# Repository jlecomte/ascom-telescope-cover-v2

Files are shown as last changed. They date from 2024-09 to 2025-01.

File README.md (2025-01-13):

# ASCOM-Compatible Telescope Cover

I do not charge anything to create and maintain these open-source projects. But if you would like to say "thanks" for this project, feel free to send any amount through Paypal using the button below. I appreciate your support!

(https://www.paypal.com/donate/?hosted_button_id=49UXY8F6VVYFA)

<!-- toc -->

- [Introduction](#introduction)
- [Finished Product](#finished-product)
- [Demo](#demo)
- [Pre-Requisites](#pre-requisites)
- [Hardware / BOM](#hardware--bom)
- [ASCOM Driver](#ascom-driver)
  * [Downloading And Installing The Driver](#downloading-and-installing-the-driver)
  * [Compiling The Driver (For Developers Only)](#compiling-the-driver-for-developers-only)
- [Arduino Firmware](#arduino-firmware)
  * [Microcontroller Compatibility](#microcontroller-compatibility)
  * [Compiling And Uploading The Firmware](#compiling-and-uploading-the-firmware)
  * [Calibration Procedure](#calibration-procedure)
- [Electronic Circuit](#electronic-circuit)
- [3D Model](#3d-model)
- [Using With NINA](#using-with-nina)
- [Known Issues](#known-issues)
  * [Device Access Synchronization](#device-access-synchronization)
- [Ideas For Improvements](#ideas-for-improvements)

<!-- tocstop -->

## Introduction

This repository contains code that allows you to build your own automated telescope cover and spectral calibrator:

* The code for the ASCOM driver (Microsoft Visual Studio 2022 project)
* The code for the Arduino firmware
* The FreeCAD 3D model
* The KiCad project for the electronic circuit

This project is an updated version of [my original ASCOM-compatible telescope cover](https://github.com/jlecomte/ascom-telescope-cover). It brings the following enhancements:

* **Analog Position Feedback:** If you happened to power up my original ASCOM-compatible telescope cover while it was not in its closed position, it would violently close because it assumed that it was in a closed position at startup. This is now fully resolved by using a servo with analog position feedback. Note that this feedback loop needs to be calibrated once.
* **Magnets:** The cover will be held in place (in either open or closed position) by magnets, which means that the servo can be powered off when it is not moving, thereby completely eliminating the possibility of vibrations while imaging.
* **PCB:** This new project uses a PCB that can be manufactured by a company like [PCB Way](https://www.pcbway.com/). This means that the final product is more compact and more reliable than when using a perforated circuit board as in my original project.
* **Spectral Calibrator:** This project includes neon bulbs that can be remotely turned on or off. This is especially useful when doing spectroscopy. **Note:** You could technically modify this project to eliminate this (if you don't need it) or replace it with an EL panel if you would like to create a motorized flat panel. I have no need for this because I have [a wireless flat panel](https://github.com/jlecomte/ascom-wireless-flat-panel) and while I do operate my equipment remotely, it is not located in a remote location (it is in my backyard, but it is nice to be able to fully control it from inside the house, or using a fully automated sequence).
* **Better 3D Model:** This new version comes with a much improved 3D model and the final product is much sturdier than my original version. It also provides a simpler and cleaner attachment method to the OTA.
* **Single Cable:** This new version only requires a USB type C cable connection for both power and data, whereas my original version required two cables (USB type C and 12V power)

## Finished Product

Here is what the finished product looks like:

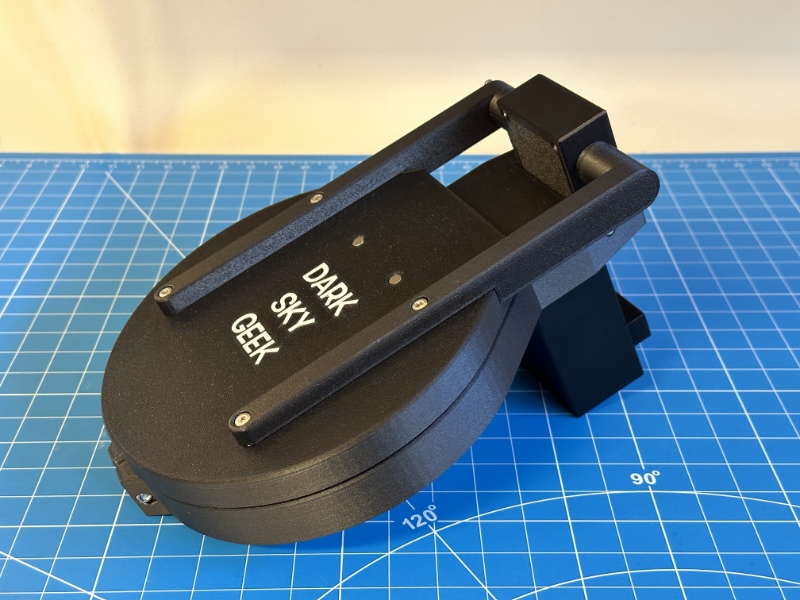
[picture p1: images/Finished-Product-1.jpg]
Finished Product


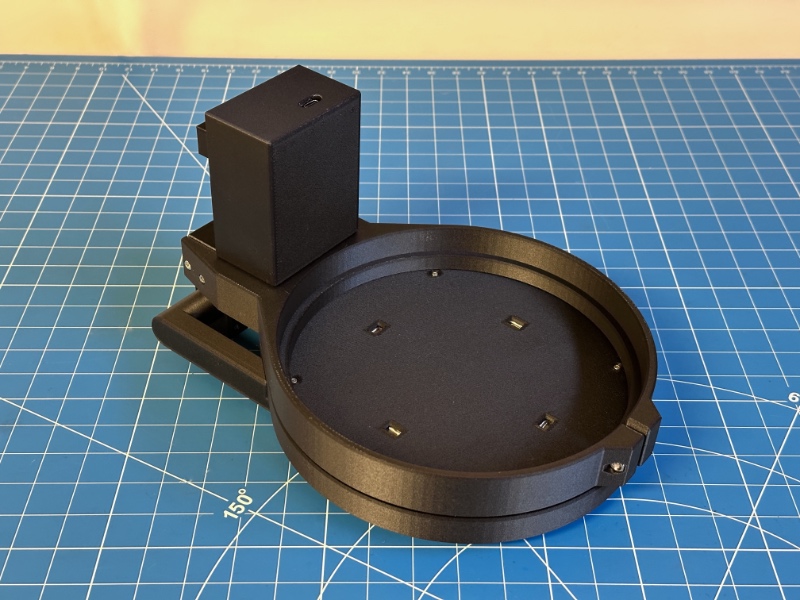
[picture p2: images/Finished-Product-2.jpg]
Finished Product


## Demo

Here is a short demo video of the finished product, hosted on YouTube. Check it out!

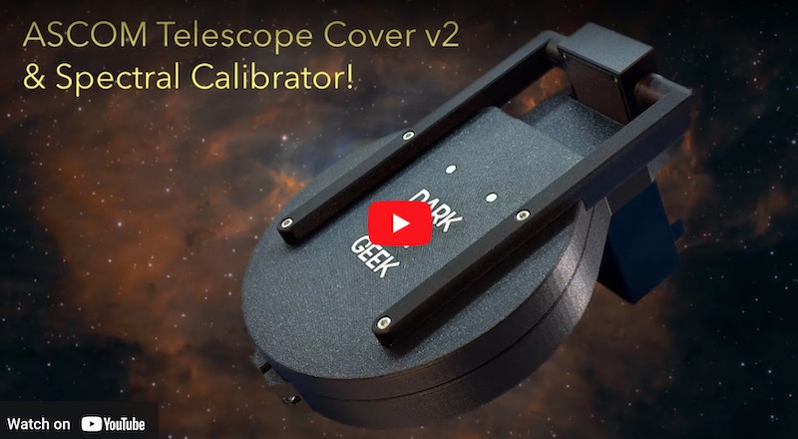
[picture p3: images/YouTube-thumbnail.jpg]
Short demo video of the finished product (https://www.youtube.com/watch?v=r8KIGEcJ2Xw)


## Pre-Requisites

* A Windows computer (Windows 10 or newer)
* [Microsoft Visual Studio](https://visualstudio.microsoft.com/) (FYI, I used the 2022 edition...)
* [ASCOM Platform 6](https://ascom-standards.org/)
* [ASCOM Platform Developer Components](https://ascom-standards.org/COMDeveloper/Index.htm)
* [Arduino IDE](https://www.arduino.cc/en/software)
* [FreeCAD](https://www.freecadweb.org/), a free and open-source 3D parametric modeler
* A 3D printer able to print PETG, and a slicer (I use a Bambu Lab X1C)
* A few basic tools that any tinkerer must own, such as [a breadboard](https://www.amazon.com/dp/B07LG9V8WQ?tag=darkskygeek-20), [a soldering iron](https://www.amazon.com/dp/B08M9B4MP4?tag=darkskygeek-20), [a bench power supply](https://www.amazon.com/dp/B07GCJ5QHF?tag=darkskygeek-20), etc.

## Hardware / BOM

* [Seeeduino XIAO](https://www.seeedstudio.com/Seeeduino-XIAO-Arduino-Microcontroller-SAMD21-Cortex-M0+-p-4426.html) (You can get it quicker from Amazon, but you will have to pay twice as much!)
* [Capacitors](https://www.amazon.com/dp/B07PBQXQNQ?tag=darkskygeek-20)
* [Resistors](https://www.amazon.com/dp/B08FD1XVL6?tag=darkskygeek-20)
* [Diodes](https://www.amazon.com/dp/B08SBTS2KZ?tag=darkskygeek-20)
* [FQP30N06L](https://www.amazon.com/dp/B07WHSD3GJ?tag=darkskygeek-20) (logic-level MOSFET)
* [EL Inverter](https://www.amazon.com/dp/B08Q7CNZ7F?tag=darkskygeek-20)
* [Neon bulbs](https://www.amazon.com/dp/B07CPY6TM5?tag=darkskygeek-20)
* [270° servo motor with analog feedback](https://www.dfrobot.com/product-1709.html)
* [8x2mm magnets](https://www.amazon.com/dp/B077KYBYYY?tag=darkskygeek-20)
* [Brass inserts for 3D printed parts](https://www.amazon.com/dp/B0BDD3865B?tag=darkskygeek-20)
* [Assortment of small metric screws, nuts, and washers](https://www.amazon.com/dp/B08JCKH31Q?tag=darkskygeek-20)

## ASCOM Driver

### Downloading And Installing The Driver

You can install the ASCOM driver by simply running the executable setup file that you will find in the [releases page](https://github.com/jlecomte/ascom-telescope-cover-v2/releases). By default, it places files under `C:\Program Files (x86)\Dark Sky Geek\Telescope Cover V2 ASCOM Driver`.

### Compiling The Driver (For Developers Only)

Open Microsoft Visual Studio as an administrator (right click on the Microsoft Visual Studio shortcut, and select "Run as administrator"). This is required because when building the code, by default, Microsoft Visual Studio will register the compiled COM components, and this operation requires special privileges (Note: This is something you can disable in the project settings...) Then, open the solution (`ASCOM_Driver\TelescopeCoverV2.sln`), change the solution configuration to `Release` (in the toolbar), open the `Build` menu, and click on `Build Solution`. As long as you have properly installed all the required dependencies, the build should succeed and the ASCOM driver will be registered on your system. The binary file generated will be `ASCOM_Driver\bin\Release\ASCOM.DarkSkyGeek.TelescopeCoverV2.dll`.

## Arduino Firmware

### Microcontroller Compatibility

Pretty much all Arduino-compatible boards should work. There is nothing magical about the firmware. However, this was developed for, and tested with a [Seeeduino XIAO](https://www.seeedstudio.com/Seeeduino-XIAO-Arduino-Microcontroller-SAMD21-Cortex-M0+-p-4426.html), so that is what I recommend for this project.

### Compiling And Uploading The Firmware

* If needed, add support for the board that you are using in your project.
* Then, connect your board to your computer using a USB cable, open the sketch file located at `Arduino_Firmware\Arduino_Firmware.ino`, and click on the `Upload` button in the toolbar.

### Calibration Procedure

This is a one-time operation. Disconnect the right arm from the servo. Then, from the Arduino IDE, connect to the device. Using the Arduino IDE serial monitor, type `COMMAND:COVER:CALIBRATE`. This will launch the calibration procedure for the servo analog feedback. Once it has completed, re-attach the right arm to the servo. The device is now ready to be used.

## Electronic Circuit

Here is the KiCad schematics:

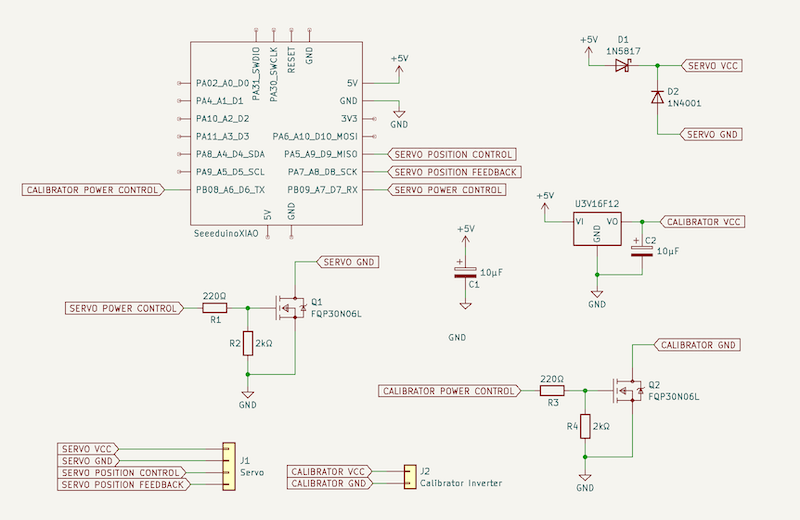
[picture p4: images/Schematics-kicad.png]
KiCad schematics


I very strongly recommend prototyping it first, using a breadboard:

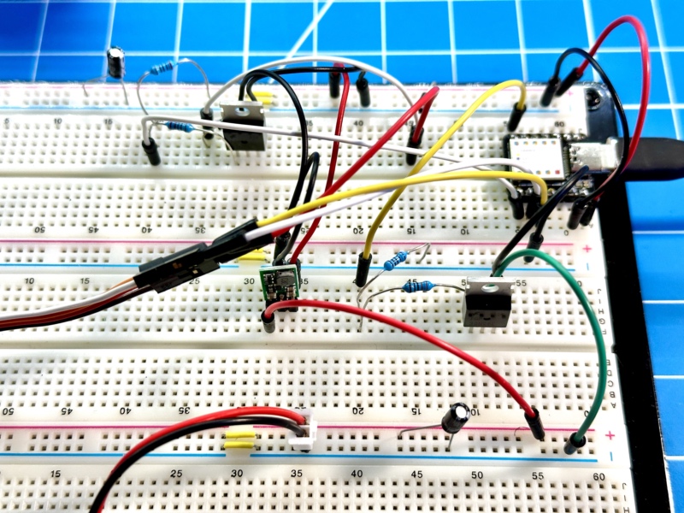
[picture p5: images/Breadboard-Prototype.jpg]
Breadboard prototype


Here is the routed PCB in KiCad:

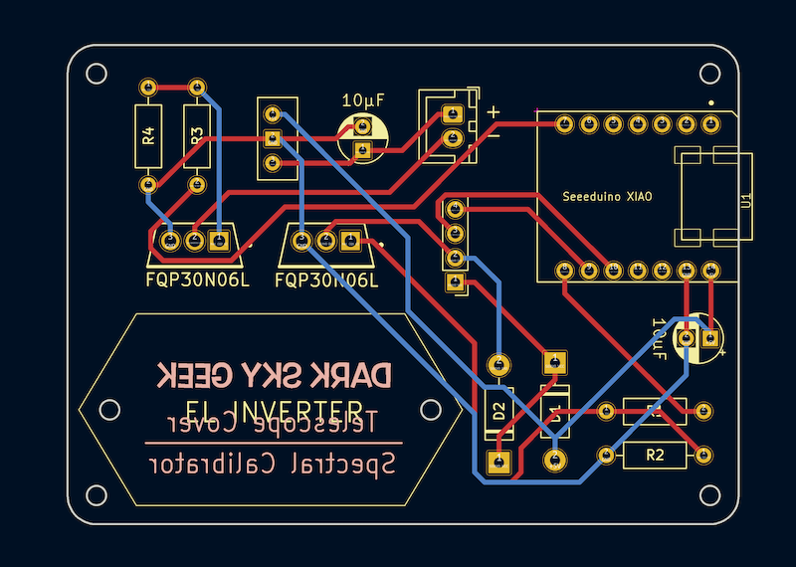
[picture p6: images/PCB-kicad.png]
Routed PCB in KiCad


**Note:** You can directly use [PCBWay.zip](KiCad_Project/PCBWay.zip) to order your PCB from [PCB Way](https://www.pcbway.com/).

Once you've received your PCB and soldered all the components, it should look like the following:

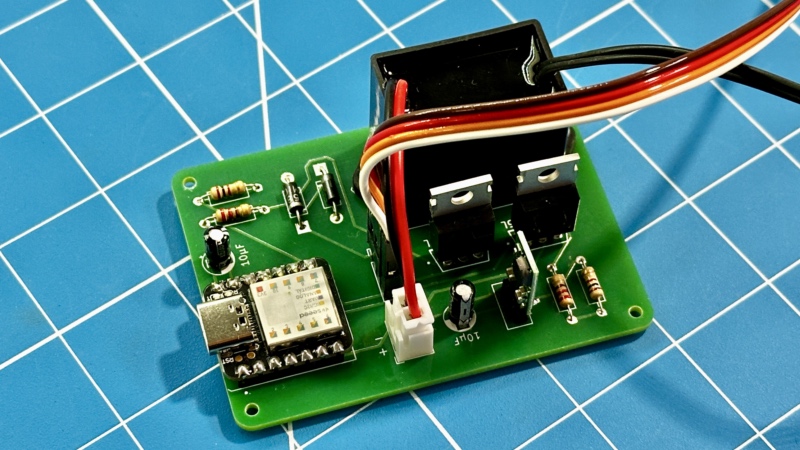
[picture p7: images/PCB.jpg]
Finished PCB


## 3D Model

:warning: **IMPORTANT:** :warning: The 3D model is parametric and will scale within a reasonable range of values for the `OTA Outside Diameter` and `OTA Thickness` pareneters (see the `Parameters` spreadsheet in the 3D model for more details...) However, FreeCAD being FreeCAD, be warned that if you change the value of a parameter multiple times, you may get a model error. Simply close the model without saving it, reopen it, and set the parameter you want to change, e.g., the `OTA Outside Diameter` parameter, to the appropriate value. The model *should* scale properly.

Here is what the 3D model looks like in FreeCAD:

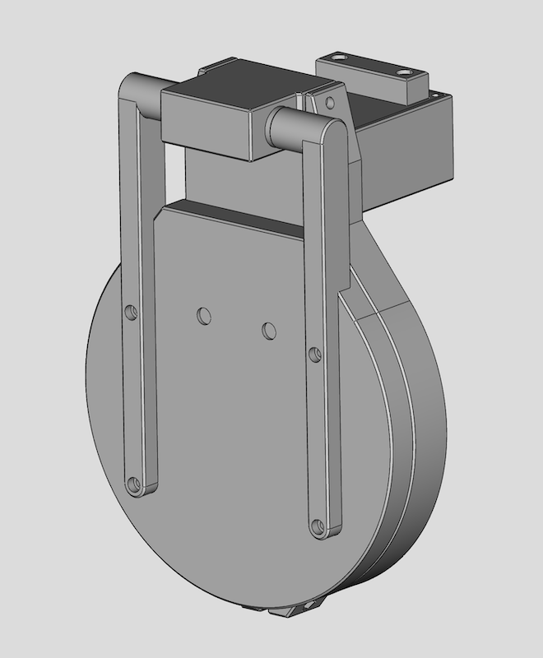
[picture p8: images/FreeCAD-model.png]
FreeCAD model


Once you've updated the model to fit your needs, you can export the parts as STL and print them on your 3D printer.

Here is how the neon bulbs are installed on the back of the cover lid:

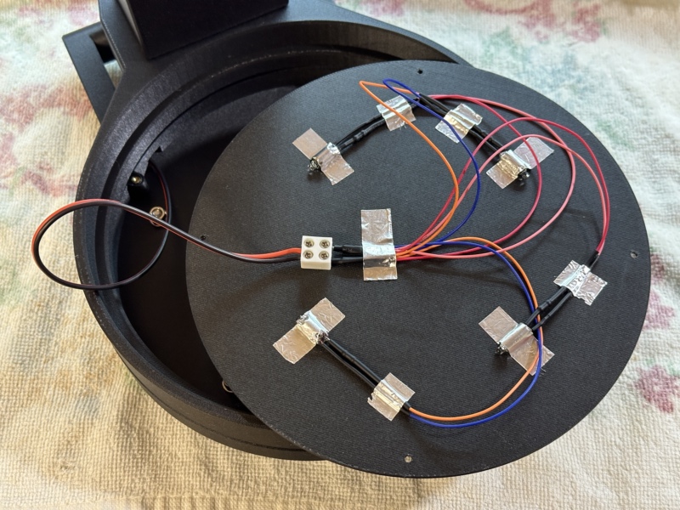
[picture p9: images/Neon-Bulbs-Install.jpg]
Neon Bulbs Install


A 47kΩ resistor is soldered to _each_ bulb, and the 4 x _resistor + bulb_ are wired in parallel (that is critical!)

The wires that power up those bulbs travel through the servo box and the left arm, so they are not directly visible, which makes for a very clean final product.

## Using With NINA

Once you have installed the driver, open NINA, go to the `Equipment` tab and select `Flat Panel`. You should be able to select the `DarkSkyGeek Telescope Cover & Spectral Calibrator` device from the device dropdown:

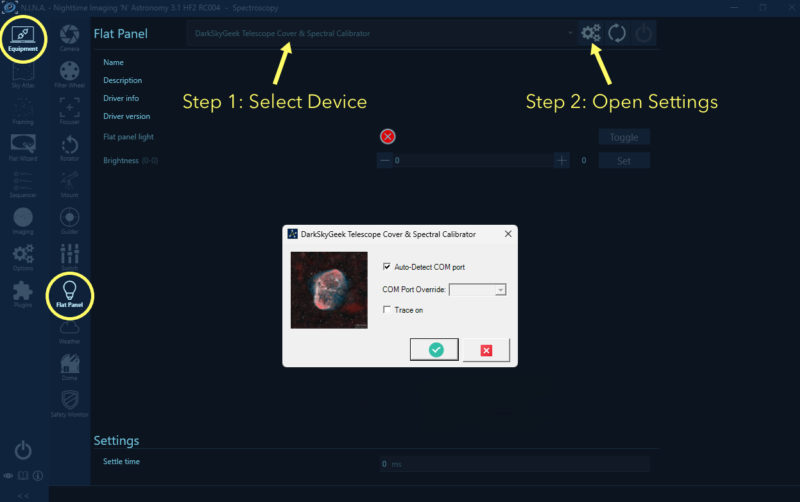
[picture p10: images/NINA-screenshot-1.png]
NINA Screenshot 1


Then, you can connect to the device, and all the standard controls should appear, allowing you to test and use your device. Enjoy!

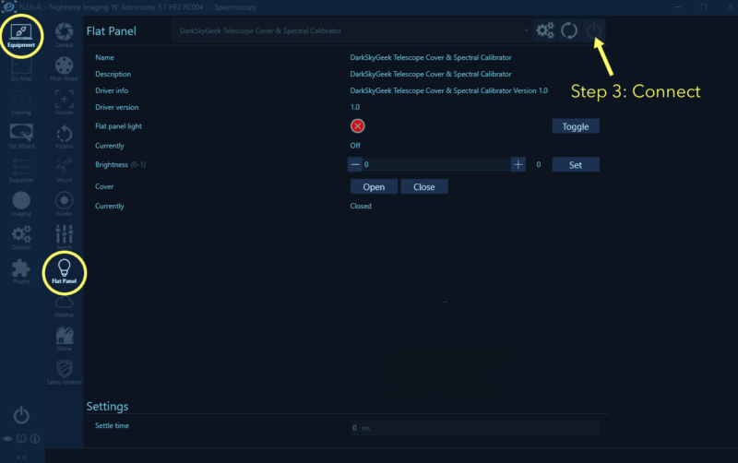
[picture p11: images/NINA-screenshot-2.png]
NINA Screenshot 2


## Known Issues

### Device Access Synchronization

I made sure that access to the serial port was synchronized, thereby preventing a second serial command from being sent if the reply to the first one has not yet been received. However, that code only works in multi-threaded applications. It will not work as expected if the same device is used by two different applications (i.e., processes) as they will each have their own instance of the ASCOM driver, and therefore their own locking object. Indeed, I opted to use the tried-and-true approach of implementing ASCOM drivers (output as a Class Library). Switching to a local COM server would have allowed me to resolve this relatively minor issue, but it seemed overkill for my use case.

## Ideas For Improvements

* Add a physical button (or several buttons) to manually control the device could be a relatively simple enhancement.
* Leverage a small embedded LiPo battery and use BLE for communication, thereby completely removing the need for a USB cable.
* Make the 3D model more scalable so that it can be easily adapted to various telescopes.

**Note:** These are just ideas for you, in case you would like to challenge yourself. I am not planning to implement any of these ideas.

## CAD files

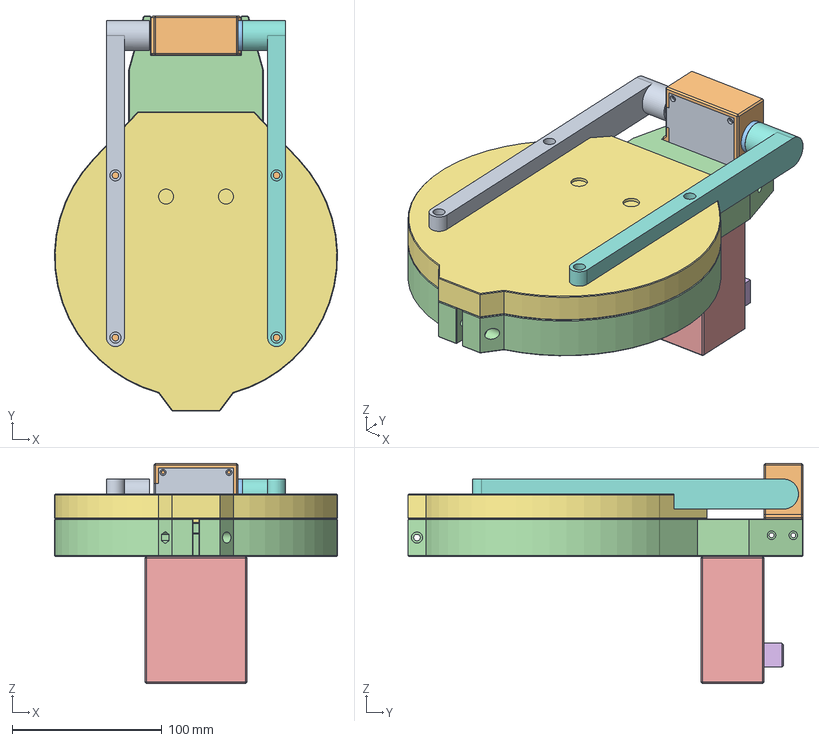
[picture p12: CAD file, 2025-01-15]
3D_Files/Cover And Spectral Calibrator - Askar 151PHQ.FCStd
188.9 x 263.6 x 147.0 mm
Servo Box Base
Servo Box Cover
Bushing
Circuit Board Box Body
Circuit Board Box Lid
Cover Outside
Left Arm
Right Arm
Cover Inside

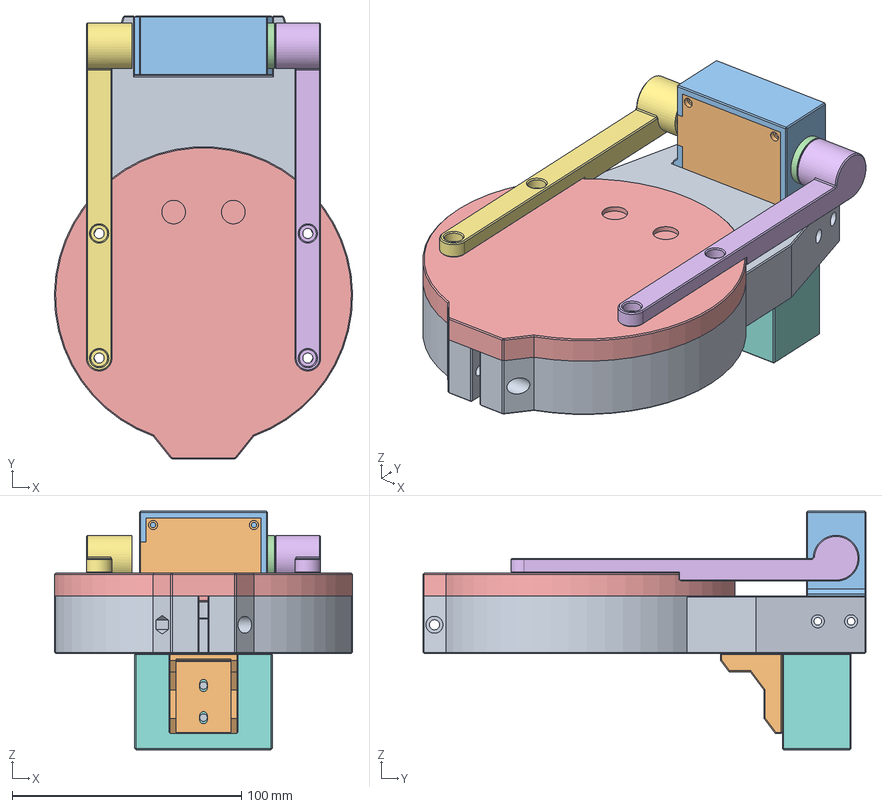
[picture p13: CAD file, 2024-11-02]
3D_Files/Cover Only - Takahashi FSQ85.FCStd
130.0 x 193.2 x 104.0 mm
Telescope-Interface-Body
Servo_Box_Base
Servo_Box_Cover
Bushing
Cover-Body
Right-Arm
Left-Arm
Circuit-Board-Box
Circuit-Board-Box-Lid
Circuit-Board-Box-Bracket

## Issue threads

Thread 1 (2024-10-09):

Change suggestion to prevent unwanted servo behavior

vef445, 2024-10-09:
Hi Julien,
First of all, thank you for sharing this new version of your motorized cover. While I'm not gonna make any use of the calibrator part of it, being able to remotely cover and uncover my two telescopes is a huge benefit for me.

When running the current release, I noticed that my servo would move (full speed) almost 90deg each time it was powered up, which is exactly what we try to avoid with using feedback.
I added some verbose to the Arduino code and noticed that when in "close" position, the value of "pos" was below 0 (around -5). Same unwanted result in "open" position, with a "pos" reporting a value above 180 (around 190).

Here is the code change that I'd like to suggest to you and which fixes the issue:

From

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

To

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

Best,
Guillaume

jlecomte, 2024-10-09:
Done, in [this commit](https://github.com/jlecomte/ascom-telescope-cover-v2/commit/044a117fa27519f7e16e70ed0cb1b7999052442b). Thanks!

Closed 2024-10-09.

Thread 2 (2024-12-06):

servo motor experiences jolts #12 - related to your archived version V1

730522js, 2024-12-06:
Hi Dark Sky Geek and many thanks for sharing your work with the community !!!

I've recently started using you Telescope Cover (v1) for which I saw you archived the repo.

I've also experienced an issue reported by user [jduffas](https://github.com/jduffas) => (servo motor experiences jolts #12) for the V1 of the telescope cover.

I'm sorry if i waste your time by opening an issue here but as that other repository (v1) was archived in Sep 2024 I though I could reach you here.

I found a workaround for the jolts of the motor and I thought to share it so perhaps somebody could make use of the workaround.

I've figured the torque does not need to be held by the code so if I disconnect the servo after each operation and reconnect it before each operation the jolts no longer occur, Here's how i changed the openCover and closeCover parts:
```
void openCover() {
    servo.attach(9); // Attach the servo to pin 9
    int pos = servo.read();

    if (pos < 180) {
        for (; pos <= 180; pos++) {
            servo.write(pos);
            delay(30); // Adjust as needed for smooth movement
        }
    }

    servo.detach(); // Detach the servo to stop holding position
    state = open;
}

void closeCover() {
    servo.attach(9); // Attach the servo to pin 9
    int pos = servo.read();

    if (pos > 0) {
        for (; pos >= 0; pos--) {
            servo.write(pos);
            delay(30); // Adjust as needed for smooth movement
        }
    }

    servo.detach(); // Detach the servo to stop holding position
    state = closed;
}
```

I hope this helps somebody.
Thanks again and take it easy!
John.

jlecomte, 2024-12-07:
`servo.read()` will not return the *real* position of the cover. It merely returns the last value passed to `servo.write()` ([reference](https://docs.arduino.cc/libraries/servo/)). Therefore, if you manually move the cover when the servo is not powered, and then power the servo (`servo.attach()` + `servo.write()`), it will most definitely jerk.

The only real way to get rid of this while still using a servo is to use what I did in the v2 of this project (i.e., in this repo), which is to use a servo with analog feedback.

Closed 2024-12-07.

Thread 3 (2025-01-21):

Have issuing with servo

giacomolorenzo, 2025-01-21:
Hi, i have printed the pcb(only cover) had assembled all but after have loaded the firmware inside the board, no have any result, the servo didn't move and the led didn't turn on, have checked the board, the led and the servo, can help me to resolve because i'm stucked from many days, (attach the image on the board )

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

have tried to send serial command to move the servo but respond not ok the servo i want to use is this

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

i had changed the servo with the link in the description but nothing was changed.

Adler6907, 2025-01-22:
it is difficult to make a satisfactory diagnosis like this.
I can only say that I recreated the same version and it worked immediately.
Was the firmware successfully installed?

giacomolorenzo, 2025-01-22:
Yes the firmware was uploaded correctly today try again with another board and send you the photo and the result of try, thank you

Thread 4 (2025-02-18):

CAD Model will not scale

sneezingdog, 2025-02-18:
I am changing the OTA to anew value 120 mm but the model will not scale. I also tried a 150 mm and had similar issues.  Also, any chance you can add the Chamfer 011 to the FSQ85 model.

Many thanks for all your hard work! It's inspiring.

zanderkent, 2025-03-01:
I was able to scale up to 120 and 150 just fine, it's scaling down that's a problem for me. I have a WO GT71 and I can't get the OTA thickness below 100mm (My OTA thickness is 92.46). If you/the author have any luck getting it smaller it would be greatly appreciated! If not I will see if I can brute force my way into it :)

sneezingdog, 2025-03-01:
I was trying to scale to 95mm, but could not do it.

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

--
Bryan Savage
707 S Lynn Street
Champaign, IL 61820

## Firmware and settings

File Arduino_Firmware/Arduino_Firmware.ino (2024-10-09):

/*
 * Arduino_Firmware.ino
 * Copyright (C) 2024 - Present, Julien Lecomte - All Rights Reserved
 * Licensed under the MIT License. See the accompanying LICENSE file for terms.
 */

#include <Servo.h>
#include <FlashStorage.h>

constexpr auto DEVICE_GUID = "55c7745e-d21a-43da-abc5-837adcb27344";

constexpr auto COMMAND_PING = "COMMAND:PING";
constexpr auto RESULT_PING = "RESULT:PING:OK:";

constexpr auto COMMAND_INFO = "COMMAND:INFO";
constexpr auto RESULT_INFO = "RESULT:DarkSkyGeek's Automated Telescope Cover And Spectral Calibrator Firmware v1.0";

constexpr auto COMMAND_COVER_OPEN = "COMMAND:COVER:OPEN";
constexpr auto RESULT_COVER_OPEN_OK = "RESULT:COVER:OPEN:OK";
constexpr auto RESULT_COVER_OPEN_NOK = "RESULT:COVER:OPEN:NOK";

constexpr auto COMMAND_COVER_CLOSE = "COMMAND:COVER:CLOSE";
constexpr auto RESULT_COVER_CLOSE_OK = "RESULT:COVER:CLOSE:OK";
constexpr auto RESULT_COVER_CLOSE_NOK = "RESULT:COVER:CLOSE:NOK";

constexpr auto COMMAND_COVER_CALIBRATE = "COMMAND:COVER:CALIBRATE";
constexpr auto RESULT_COVER_CALIBRATE_OK = "RESULT:COVER:CALIBRATE:OK";

constexpr auto COMMAND_COVER_GET_CALIBRATION = "COMMAND:COVER:GETCALIBRATION";
constexpr auto RESULT_COVER_GET_CALIBRATION = "RESULT:COVER:GETCALIBRATION:";

constexpr auto COMMAND_COVER_GETSTATE = "COMMAND:COVER:GETSTATE";
constexpr auto RESULT_COVER_STATE_OPENING = "RESULT:COVER:GETSTATE:OPENING";
constexpr auto RESULT_COVER_STATE_OPEN = "RESULT:COVER:GETSTATE:OPEN";
constexpr auto RESULT_COVER_STATE_CLOSING = "RESULT:COVER:GETSTATE:CLOSING";
constexpr auto RESULT_COVER_STATE_CLOSED = "RESULT:COVER:GETSTATE:CLOSED";

constexpr auto COMMAND_CALIBRATOR_ON = "COMMAND:CALIBRATOR:ON";
constexpr auto RESULT_CALIBRATOR_ON = "RESULT:CALIBRATOR:ON:OK";

constexpr auto COMMAND_CALIBRATOR_OFF = "COMMAND:CALIBRATOR:OFF";
constexpr auto RESULT_CALIBRATOR_OFF = "RESULT:CALIBRATOR:OFF:OK";

constexpr auto COMMAND_CALIBRATOR_GETSTATE = "COMMAND:CALIBRATOR:GETSTATE";
constexpr auto RESULT_CALIBRATOR_STATE_ON = "RESULT:CALIBRATOR:GETSTATE:ON";
constexpr auto RESULT_CALIBRATOR_STATE_OFF = "RESULT:CALIBRATOR:GETSTATE:OFF";

constexpr auto ERROR_INVALID_COMMAND = "ERROR:INVALID_COMMAND";

// Pins assignment. Change these depending on your exact wiring!
const unsigned int CALIBRATOR_SWITCH_PIN = 6;
const unsigned int SERVO_SWITCH_PIN = 7;
const unsigned int SERVO_FEEDBACK_PIN = 8;
const unsigned int SERVO_CONTROL_PIN = 9;

// Value used to determine whether the NVM (Non-Volatile Memory) was written,
// or we are just reading garbage...
const unsigned int NVM_MAGIC_NUMBER = 0x12345678;

enum CoverState {
  opening,
  open,
  closing,
  closed
} coverState;

enum CalibratorState {
  on,
  off
} calibratorState;

typedef struct {
  unsigned int magicNumber;
  double slope;
  double intercept;
} ServoCalibration;

FlashStorage(nvmStore, ServoCalibration);

Servo servo;
ServoCalibration servoCalibrationData;

// How long do we wait between each step in order to achieve the desired speed?
const unsigned long STEP_DELAY_MICROSEC = 30L * 1000; // 30 msec

// Variables used to move the servo in the main loop...
int servo_position;
unsigned long last_step_time;

void setup() {
  // Initialize serial port I/O.
  Serial.begin(57600);
  while (!Serial) {
    ;  // Wait for serial port to connect. Required for native USB!
  }
  Serial.flush();

  // Read servo calibration data oin Flash storage:
  servoCalibrationData = nvmStore.read();

  // Initialize pins...
  pinMode(CALIBRATOR_SWITCH_PIN, OUTPUT);
  pinMode(SERVO_SWITCH_PIN, OUTPUT);
  pinMode(SERVO_FEEDBACK_PIN, INPUT);
  pinMode(SERVO_CONTROL_PIN, OUTPUT);

  // Make sure the RX, TX, and built-in LEDs don't turn on, they are very bright!
  // Even though the board is inside an enclosure, the light can be seen shining
  // through the small opening for the USB connector! Unfortunately, it is not
  // possible to turn off the power LED (green) in code...
  pinMode(PIN_LED_TXL, INPUT);
  pinMode(PIN_LED_RXL, INPUT);
  pinMode(LED_BUILTIN, OUTPUT);
  digitalWrite(LED_BUILTIN, HIGH);

  // Make sure the servo is initially de-energized...
  digitalWrite(SERVO_SWITCH_PIN, LOW);

  // Make sure the calibrator is initially turned off...
  digitalWrite(CALIBRATOR_SWITCH_PIN, LOW);
  calibratorState = off;

  servo_position = 0;
  last_step_time = 0L;

  // When there is no calibration data yet, we have to assume that the cover is closed...
  if (servoCalibrationData.magicNumber != NVM_MAGIC_NUMBER) {
    coverState = closed;
  } else {
    // Close the cover, in case it is not completely closed.
    // To make sure that `closeCover` does not have an undefined behavior,
    // we initialize the `coverState` variable to `open`, just in case.
    // That variable will be updated in the `closeCover` function,
    // and then again once the cover has completely closed.
    coverState = open;
    closeCover(false);
  }
}

void loop() {
  if (Serial.available() > 0) {
    String command = Serial.readStringUntil('\n');
    if (command == COMMAND_PING) {
      handlePing();
    } else if (command == COMMAND_INFO) {
      sendFirmwareInfo();
    } else if (command == COMMAND_COVER_GETSTATE) {
      sendCurrentCoverState();
    } else if (command == COMMAND_COVER_OPEN) {
      openCover(true);
    } else if (command == COMMAND_COVER_CLOSE) {
      closeCover(true);
    } else if (command == COMMAND_COVER_CALIBRATE) {
      calibrateCover();
    } else if (command == COMMAND_CALIBRATOR_GETSTATE) {
      sendCurrentCalibratorState();
    }else if (command == COMMAND_CALIBRATOR_ON) {
      turnCalibratorOn();
    } else if (command == COMMAND_CALIBRATOR_OFF) {
      turnCalibratorOff();
    } else if (command == COMMAND_COVER_GET_CALIBRATION) {
      sendCalibrationData();
    } else {
      handleInvalidCommand();
    }
  }

  // Blink the built-in LED to let the user know that the device needs to be calibrated once!
  // Note: The device needs to be recalibrated every time the firmware is flashed.
  if (servoCalibrationData.magicNumber != NVM_MAGIC_NUMBER) {
    digitalWrite(LED_BUILTIN, HIGH);
    delay(500);
    digitalWrite(LED_BUILTIN, LOW);
    delay(500);
  }

  if (coverState == opening || coverState == closing) {
    // Make sure we don't prematurely take a step if it's too early...
    unsigned long now = micros();
    if (now - last_step_time >= STEP_DELAY_MICROSEC) {
      last_step_time = now;

      if (coverState == opening) {
        servo_position++;
        if (servo_position >= 180) {
          servo_position = 180;
          coverState = open;
        }
      } else if (coverState == closing) {
        servo_position--;
        if (servo_position <= 0) {
          servo_position = 0;
          coverState = closed;
        }
      }

      servo.write(servo_position);

      if (coverState == open || coverState == closed) {
        powerDownServo();
      }
    }
  }
}

void handlePing() {
  Serial.print(RESULT_PING);
  Serial.println(DEVICE_GUID);
}

void sendFirmwareInfo() {
  Serial.println(RESULT_INFO);
}

void sendCurrentCoverState() {
  switch (coverState) {
    case opening:
      Serial.println(RESULT_COVER_STATE_OPENING);
      break;
    case open:
      Serial.println(RESULT_COVER_STATE_OPEN);
      break;
    case closing:
      Serial.println(RESULT_COVER_STATE_CLOSING);
      break;
    case closed:
      Serial.println(RESULT_COVER_STATE_CLOSED);
      break;
  }
}

void openCover(bool writeResultToSerial) {
  if (servoCalibrationData.magicNumber != NVM_MAGIC_NUMBER || (coverState != closed && coverState != closing)) {
    if (writeResultToSerial) {
      Serial.println(RESULT_COVER_OPEN_NOK);
    }
    return;
  }

  servo_position = powerUpServo();
  coverState = opening;

  if (writeResultToSerial) {
    Serial.println(RESULT_COVER_OPEN_OK);
  }
}

void closeCover(bool writeResultToSerial) {
  if (servoCalibrationData.magicNumber != NVM_MAGIC_NUMBER || (coverState != open && coverState != opening)) {
    if (writeResultToSerial) {
      Serial.println(RESULT_COVER_CLOSE_NOK);
    }
    return;
  }

  servo_position = powerUpServo();
  coverState = closing;

  if (writeResultToSerial) {
    Serial.println(RESULT_COVER_CLOSE_OK);
  }
}

void calibrateCover() {
  Serial.println(RESULT_COVER_CALIBRATE_OK);

  powerUpServo();

  int step = 10;
  int nDataPoints = 1 + 180 / step;

  double x[nDataPoints] = { 0 };
  double y[nDataPoints] = { 0 };

  for (int i = 0, pos = 0; pos <= 180; i++, pos = i * step) {
    servo.write(pos);
    delay(1000);
    int feedbackValue = analogRead(SERVO_FEEDBACK_PIN);
    x[i] = pos;
    y[i] = feedbackValue;
  }

  linearRegression(x, y, nDataPoints, &servoCalibrationData.slope, &servoCalibrationData.intercept);
  servoCalibrationData.magicNumber = NVM_MAGIC_NUMBER;
  nvmStore.write(servoCalibrationData);

  coverState = open;

  closeCover(false);
}

void sendCalibrationData() {
  Serial.print(RESULT_COVER_GET_CALIBRATION);
  if (servoCalibrationData.magicNumber != NVM_MAGIC_NUMBER) {
    Serial.println("0:0");
  } else {
    Serial.print(servoCalibrationData.slope);
    Serial.print(":");
    Serial.println(servoCalibrationData.intercept);
  }
}

void sendCurrentCalibratorState() {
  switch (calibratorState) {
    case on:
      Serial.println(RESULT_CALIBRATOR_STATE_ON);
      break;
    case off:
      Serial.println(RESULT_CALIBRATOR_STATE_OFF);
      break;
  }
}

void turnCalibratorOn() {
  digitalWrite(CALIBRATOR_SWITCH_PIN, HIGH);
  calibratorState = on;
  Serial.println(RESULT_CALIBRATOR_ON);
}

void turnCalibratorOff() {
  digitalWrite(CALIBRATOR_SWITCH_PIN, LOW);
  calibratorState = off;
  Serial.println(RESULT_CALIBRATOR_OFF);
}

void handleInvalidCommand() {
  Serial.println(ERROR_INVALID_COMMAND);
}

// Energize and attach servo.
int powerUpServo() {
  digitalWrite(SERVO_SWITCH_PIN, HIGH);

  // Default position (closed), which will be used only once,
  // before we have successfully calibrated the servo.
  int pos = 0;

  if (servoCalibrationData.magicNumber == NVM_MAGIC_NUMBER) {
    // Short delay, so that the servo has been fully initialized.
    // Not 100% sure this is necessary, but it won't hurt.
    delay(100);

    int feedbackValue = analogRead(SERVO_FEEDBACK_PIN);
    pos = (int)((feedbackValue - servoCalibrationData.intercept) / servoCalibrationData.slope);

    // Deal with slight errors in the calibration process...
    if (pos < 0) {
      pos = 0;
    } else if (pos > 180) {
      pos = 180;
    }
  }

  // This step is critical! Without it, the servo does not know its position when it is attached below,
  // and the first write command will make it jerk to that position, which is what we want to avoid...
  servo.write(pos);

  // The optional min and max pulse width parameters are actually quite important
  // and depend on the exact servo you are using. Without specifying them, you may
  // not be able to use the full range of motion (270 degrees for this project)
  servo.attach(SERVO_CONTROL_PIN, 500, 2500);

  return pos;
}

// Detach and de-energize servo to eliminate any possible sources of vibrations.
// Magnets will keep the cover in position, whether it is open or closed.
void powerDownServo() {
  servo.detach();
  digitalWrite(SERVO_SWITCH_PIN, LOW);
}

// Function to calculate the mean of an array.
double mean(double arr[], int n) {
    double sum = 0.0;
    for (int i = 0; i < n; i++) {
        sum += arr[i];
    }
    return sum / n;
}

// Function to calculate the slope and intercept of a linear regression line.
void linearRegression(double x[], double y[], int n, double *slope, double *intercept) {
    double x_mean = mean(x, n);
    double y_mean = mean(y, n);
    double numerator = 0.0;
    double denominator = 0.0;
    for (int i = 0; i < n; i++) {
        numerator += (x[i] - x_mean) * (y[i] - y_mean);
        denominator += (x[i] - x_mean) * (x[i] - x_mean);
    }
    *slope = numerator / denominator;
    *intercept = y_mean - (*slope * x_mean);
}

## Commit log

2024-10-09 Deal with slight errors in calibration
    [Arduino_Firmware.ino]
2024-11-02 Added FSQ85 model and simple PCB
    [Cover And Spectral Calibrator - Askar 151PHQ.FCStd, Cover Only - Takahashi FSQ85.FCStd, TelescopeCoverV2-Simple.kicad_sch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]
2025-01-13 Made the 3D model patrametric and able to scale
    [Cover And Spectral Calibrator - Askar 151PHQ.FCStd]
2025-01-15 Changed some magnets to be 6mm diameter
    [Cover And Spectral Calibrator - Askar 151PHQ.FCStd]
2025-01-15 Changed 6mm magnet holes to be 2mm deep
    [Cover And Spectral Calibrator - Askar 151PHQ.FCStd]
